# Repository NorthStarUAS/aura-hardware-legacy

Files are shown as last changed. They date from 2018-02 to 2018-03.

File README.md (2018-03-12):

# AuraUAS Autopilot Hardware

This is a repository of hardware designs that have evolved out of the
AuraUAS project.  These designs serve the AuraUAS ecosystem.

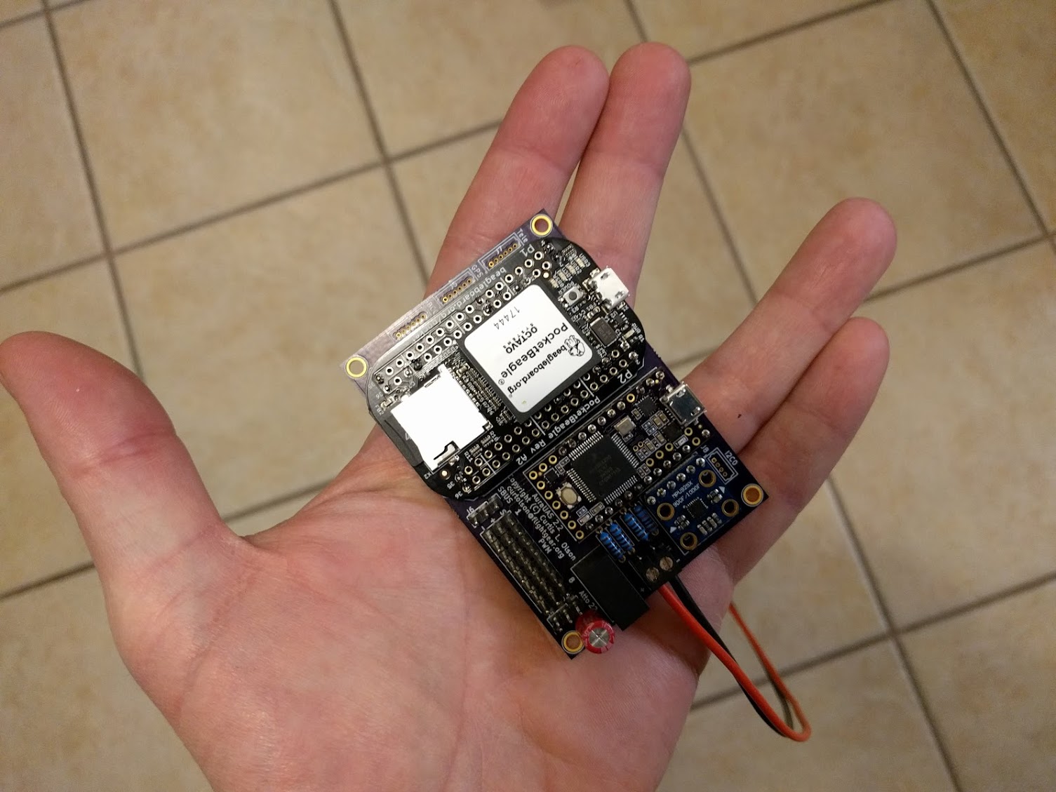
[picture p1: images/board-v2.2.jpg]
map Version 2.2 Build


## Version 1.0 - 1.4 (May 2015 - August 2016)

Beaglebone Black + Custom Cape + APM2

This is the first functional autopilot board design I created myself.
I have built up at least 4 flying autopilots from this design.
However, it leverages the old APM2 (atmega2560-based) board as the
sensor head.  This results actually are quite good, but it leads to a
stack of 3 boards and a fairly inefficient layout.  Also the APM2 is a
very old design now, has some limitations, and is only available through
clone outlets.

## Version 1.5 (January 2017)

Beaglebone Black + Custom Cape + Teensy-3.2

Although not listed as v1.5 in the file names, this is the logical
successor to the APM2-based board.  The APM2 is dropped and replaced
by a more modern teensy-3.2 paired with an IMU/Pressure breakout
board.  The teensy offers much more CPU power, more memory, better
ADC's, and native 3.3v ttl logic levels.

The system was breadboarded and the overall concept proved out.
However, before this design was finished or built, the pocketbeagle
became available.  This has prompted me to move to the next iteration.

## Version 2.0 - 2.1 (January 2018)

Pocketbeagle + Teensy-3.2 + Custom Board (designed with Express PCB)

This is a single board that combines a pocketbeagle + teensy + imu
breakout + voltage regulator + connectors in a single board package
that has only slightly larger footprint compared to the original
beaglebone.

I ordered a test run of the v2.0 board and built up one to full flight
status.

This board was designed with the Express PCB software which also
requires ordering your boards from Express PCB.  The trade off is ease
of design versus flexibility and cost.

## Version 2.2 (February 2018)

Pocketbeagle + Teensy-3.2 + Custom Board (KiCad + Oshpark)

The next evolution of the board is a redesign in KiCad.  The main
benefit is the ability to order the design from a multitude of board
houses, and possibly even do a pick and place shop at some point in
the future.  This gives the most flexibility and less expensive board
runs.

Oshpark is a great inexpensive option.  They can suck in my KiCad pcb
file directly, and they are open-source and community-sharing
friendly.

Major updates:
- Switch to the awesome KiCad PCB design tool.
- Rearrange and move some parts to shrink the board footprint and
  simplify trace routing.
- Cleans up a few small goof ups in the v2.0 design.
- Switch to the TSR2-2450 power supply (functionally similar but
  slimmer and cleaner looking.)
- Add a voltage divider/sensor circuit for main input battery voltage
  (to complement the regulated voltage sensor.)
- Switch to a robust screw terminal connector for main power.

## Version 2.3 (March 2018)

Pocketbeagle + Teensy-3.2 + 2 Layer Custom Board (KiCad + Oshpark)

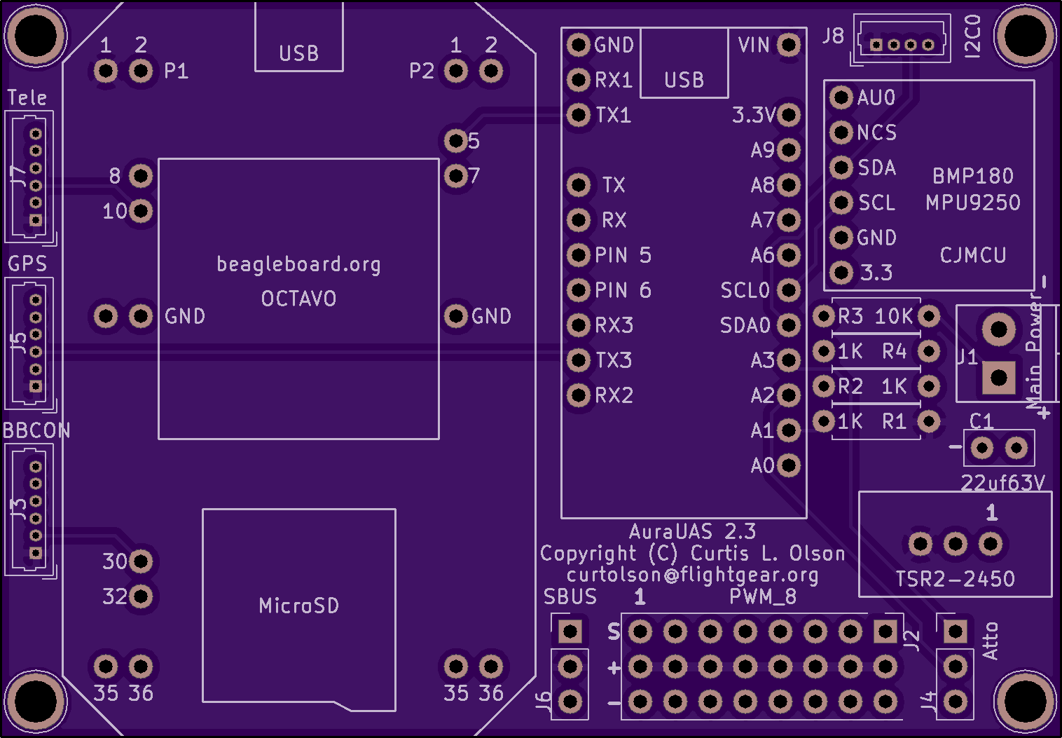
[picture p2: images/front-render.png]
map Front of board


Major updates:
- Reverse TX/RX on GPS and Telemetry ports to match drone code
  standard (big dohhh!!! while assembling the first v2.2 board)
- Slide screw terminal slightly towards board edge to give more space
  to the resistors.
- Clearly mark pin 1 on TSR2-2450 connector to help avoid assembly
  mistakes.
- Relocate capacitor away from corner mounting hole.
- Draw bigger usb port outlines on teensy/pocketbeagle to match reality.
- Space sbus and atto connectors exactly 0.2" from ends of PWM block.-
  Experiment with KiCad's autorouting feature.
- Many small component placement and trace routing adjustments for better
  fit and aethsetics.

## Overview

These board designs support the AuraUAS autopilot flight code and
firmware.  The goal is to offer a relatively simple DIY "kit build"
solution for fixed wing UAV autopilots.  Attention is put towards
using inexpensive, but powerful off the shelf components.  Assembly is
relatively simple (mostly 0.1" header soldering.)  Overall cost is
comparable to other small UAV autopilot systems.

The basic architecture of the system employs a 'little' processor and
a 'big' processor working together as a distributed system.  The
little processor handles all the hard real time sensor I/O tasks.  The
big processor does all the heavy lifting, ekf, control, navigation,
logging, communication, and higher level logic and functions.

This system has been developed based on experience with UAS flight
control hardware, software, and flight test experience starting around
2005.  There is a fair bit of thought, experience, different ideas
tried, and lessons learned the hard way that have gone into the design
choices, development, and tuning of this system.

The following information needs to be reviewed and updated, but is
still mostly reliable.

## Primary design goals

- Maximize use of existing mature, inexpensive, and widely available
  sub-components.
- Minimize amount of custom electronic circuits, soldering, and cabling.
- Easy assembly/fabrication from kit (mostly 0.1" header soldering.)
- Minimize external wiring rats nest by pushing as many connections as
  possible onto the cape.
- High performance, high reliability, production quality flight
  results.

## Features

- Beaglebone/Linux based flight control system (big processor).
- Teensy/arduino based sensor interface (little processor.)
- SBUS RC Inputs (SBUS receiver required)
- 8 PWM Outputs (PWM servos required)
- MPU-9250 IMU, BMP[12]80 pressure sensor.
- 5v 2A power regulator on board.
- Attopilot (volt/amp) sensor interface for main battery.
- Avionics/main voltage sensing on board.
- Pocketbeagle console UART exposed.
- Supports industry standard (mRo) external devices: ublox 8 gps,
  900mhz radio modem, i2c based airspeed sensor.
- Mature firmware, autopilot flight code, and ground station interface.

## Power

- Input power can be anything that ranges from 6.5-36 volts.
- The board includes a 5V 2A regulator to provide clean stable power
  for all the avionics (pocketbeagle, teensy, gps, telemetry, RC
  receiver, etc.)
- Servos are powered from some external source arranged by the
  integrator (for example from the ESC via the throttle channel.)

## Communication

- Supports a variety of 5v (3.3v TTL) radio modems such as Freescale,
  mRo, and Digi Xtend.
- Exposes the mini-usb port on both the Teensy and the Pocketbeagle
  for updating firmware or debugging.
- Exposes the beaglebone UART0 (console) for additional communication
  and/or debugging the beaglebone.

## Cost

This board is not available for sale as an assembled unit.  However,
you are welcome to download the design and order it through Oshpark
(or any other board service.)  You can purchase all the components and
populate the board yourself with only minimal soldering skills.  I
estimate it will cost about $100/ea to assemble a full board.  Most
items can be purchased with free shipping.

The external components such as gps, radio modem, receiver, attopilot
volt/current sensor, etc. need to be purchased separately.  These are
things that are required for any autopilot system.

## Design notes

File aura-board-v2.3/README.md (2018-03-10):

# AuraUAS Autopilot Board

## Assembly Instructions and Check List

I recommend you print out these instructions on paper and actually
check off each step as it is completed.  Some steps cannot be
completed out of order!  If you work carefully and don't need to
resolve any major goof ups, I think most people can do this assembly in
2-3 evenings.

### Tools required

- [ ] A nice solder station such as a Weller WES51.  Right now I like
  600-650F for soldering 0.1" header pins.
- [ ] A volt meter and continuity checker.
- [ ] A small clipping pliers / wire cutter.
- [ ] Needle nose pliers.
- [ ] Lighted magnifying lens (if over 40.)
- [ ] 6.5 - 36V power supply.  I have a bench power supply from Extech
  that allows me to vary the voltage and shows me the current draw,
  but a battery or simple wall wart could work fine too.

### Install Power Subsystem

- [ ] Install 3.5mm screw terminal block.
- [ ] Install TSR2-2450 voltage regulator.  Note: pin 1 on the
  TSR2-2450 has a white dot next to it.  This corresponds with the
  hole nearest the edge of the board.
- [ ] You can go ahead and power up the board at this point (I
  recommend using < 20 volt supply until the capacitor is installed.)
  Using the schematic and board layout, test all the 5v points to make
  sure power is getting to the correct locations.
- [ ] Install the 22uf63v capacitor being careful to note polarity.
- [ ] Install the 3 x 1k ohm resistors. You might find a needle nose
  pliers helpful to gently pull on the wires from the back side and
  help the resister fully seat in place.
- [ ] Install the 10k ohm resistor.  Polarity does not matter with
  resistors.  Clip off the excess wire from the back of the board.
- [ ] Go ahead and power up the board again.  Test that pin-hole A0 on
  the teensy footprint reads about 1/11 of your input voltage.  Test
  that pin-hole A1 reads about 2.5 volts.

### Install the Teensy-3.2

- [ ] Carefully scratch between the two pads on the reverse side of
  the board to disable USB power to the teensy.  This is important
  because the teensy-3.2 is not tolerant of being powered by both usb
  and onboard power simultaneously.
  - If you forget this step before installing the teensy, there is no
    way to fix it!  But there is a work around ...
  - The recommendation is to rig up a standard USB cable with
    the red power line snipped and still safely upload firmware to your
    teensy while it is powered by the board regulator.
  - It is just annoying because you have to remember to use the
    correct usb cable or you may significantly shorten the life of your
    teensy.
  - I recommend you clearly mark the usb port on the teensy to remind
    yourself to always use your special non-power usb cable.
- [ ] Clip rows of 0.1" header pins to fill the available holes
  between the teensy and the AuraUAS board.
- [ ] Test fit the teensy, making sure you are not shifted up or down
  by one pin.  The teensy should be centered on the footprint outline
  drawn on the board.  The teensy usb port should be at the top edge
  of the board as shown in the footprint outline.
- [ ] Carefully solder all the pins from the top side.
- [ ] Last chance!  Make sure you scratched apart the two pads on the
  bottom of the teensy.
- [ ] Flip the board over and carefully solder all the pins from the
  bottom side.
- [ ] Use your wire cutter to carefully clip all the excess length of
  the back side pins off the board.
- [ ] Power up the board.  A stock teensy should blink it's LED light
  about once per second if it is getting power properly.
- [ ] Test that you are reading 3.3 volts at the MPU-9250 breakout
  board 3.3 pin hole.
- [ ] You can install the teensy-3.2 firmware (aura-sensors) now if
  you wish or wait until later.

### Install the CJMCU MPU-9250 breakout board

- [ ] Follow the same basic technique used for the teensy.
- [ ] Clip a continuous row of 5 x 0.1" header pins (The breakout
  board may come with pins.)
- [ ] Carefully position the board (supporting the side opposite of
  the pins with a spare header pin on it's side) and solder the pins
  from the top of the board. Note that it may be a tight fit depending
  on which board you get.
- [ ] Flip the board over and solder the back side pins.  *Important:*
  be careful to ensure the breakout board is as flush as possible and
  square with the AuraUAS board. Your IMU is on this board so it the
  more accurately you place this board, the better life will be when
  it comes time to fly.
- [ ] Don't forget to clip off the excess pin material on the back
  side of the board.
- [ ] Now you can power up the board and test the firmware is able to
  read the IMU!

### Install the Pocketbeagle

- [ ] Follow the same basic procedure as the teensy and the IMU
  breakout boards.
- [ ] Clip individual and pair-wise 0.1" pins to fill in the pin-holes
  that are used by the teensy.  8 x 2-pin pairs + 1 individual pin is needed.
- [ ] Carefully position the pocketbeagle on the board.  Before
  soldering, make sure the pocketbeagle is lined up with the footprint
  lines, the usb port is facing the top side of the board, and that
  there are no missing pins.  Now go ahead and solder the pins from
  the top side.
- [ ] Flip the board over and solder the pins from the backside.  Then
  clip off the excess pin length.
- [ ] Go ahead and power the board up again.  The pocketbeagle has a
  blue led that should light up.
- [ ] If you have an SD card prepared, you can insert it and fully
  boot up the pocketbeagle, connect to a laptop via the usb port, log
  in like it's any other beaglebone in the world, and you should be do
  all sorts of linux stuff.

### Install the RC Connectors

- [ ] Clip off 3 strings of 8 x 0.1" headers to complete the PWM
  output block.  Solder these on from the back.  A servo connector
  plugged into one or both ends can really help keep their alignment
  right on while you solder them in.
- [ ] Clip off 2 strings of 3 x 0.1" headers for the SBUS input
  connector and the Attopilot connector.  Solder these in.  I often try
  to block up the connector is it is positioned correctly.  Then I
  solder one pin and check for position and alignment.  If anything is
  off I can reheat that one pin and fix it.  Then once everything is
  double checked good and lined up and in the right place, I finish
  soldering the remainder of the pins.

### Install the Picoblade (or DF-13) connectors.

Integrator's choice of connectors here.  Sorry that JST-GH doesn't
have a through-hole variant so we are stuck with one of these other
connectors.  mRobotics should have JST-GH -> Picoblade and JSG-GH ->
DF-13 cables available, so pick your favorite and go with it.

These connectors have 1.25mm spacing so they are a bit trickier than
the 0.1" inch connectors.  Just be super careful, use a small bit of
solder, and remember heat and surface tension should make the solder
go where it needs to go and no further.  Be careful not to slather in
too much solder and bridge two adjacent pins!

Again, I recommend doing your best to block up and align the
connector, then solder just one pin.  Carefully check position and
alignment.  It's easy to reheat that one pin and make adjustments.
When you are happy, solder the remaining pins.

- [ ] Install the 6-position telemetry and gps connectors.  (Note the
  board can support soldering a 5-position connector.  You can review
  the schematic and board layout to figure out the proper position.)
- [ ] Install the 4-position i2c connector.  Again, mRobotics is your
  cable adapter friend.
- [ ] Optionally install the 6-position BBCON connector.  This gives
  you access to the Pocketbeagle console for debugging or possibly
  another uart for some future use.

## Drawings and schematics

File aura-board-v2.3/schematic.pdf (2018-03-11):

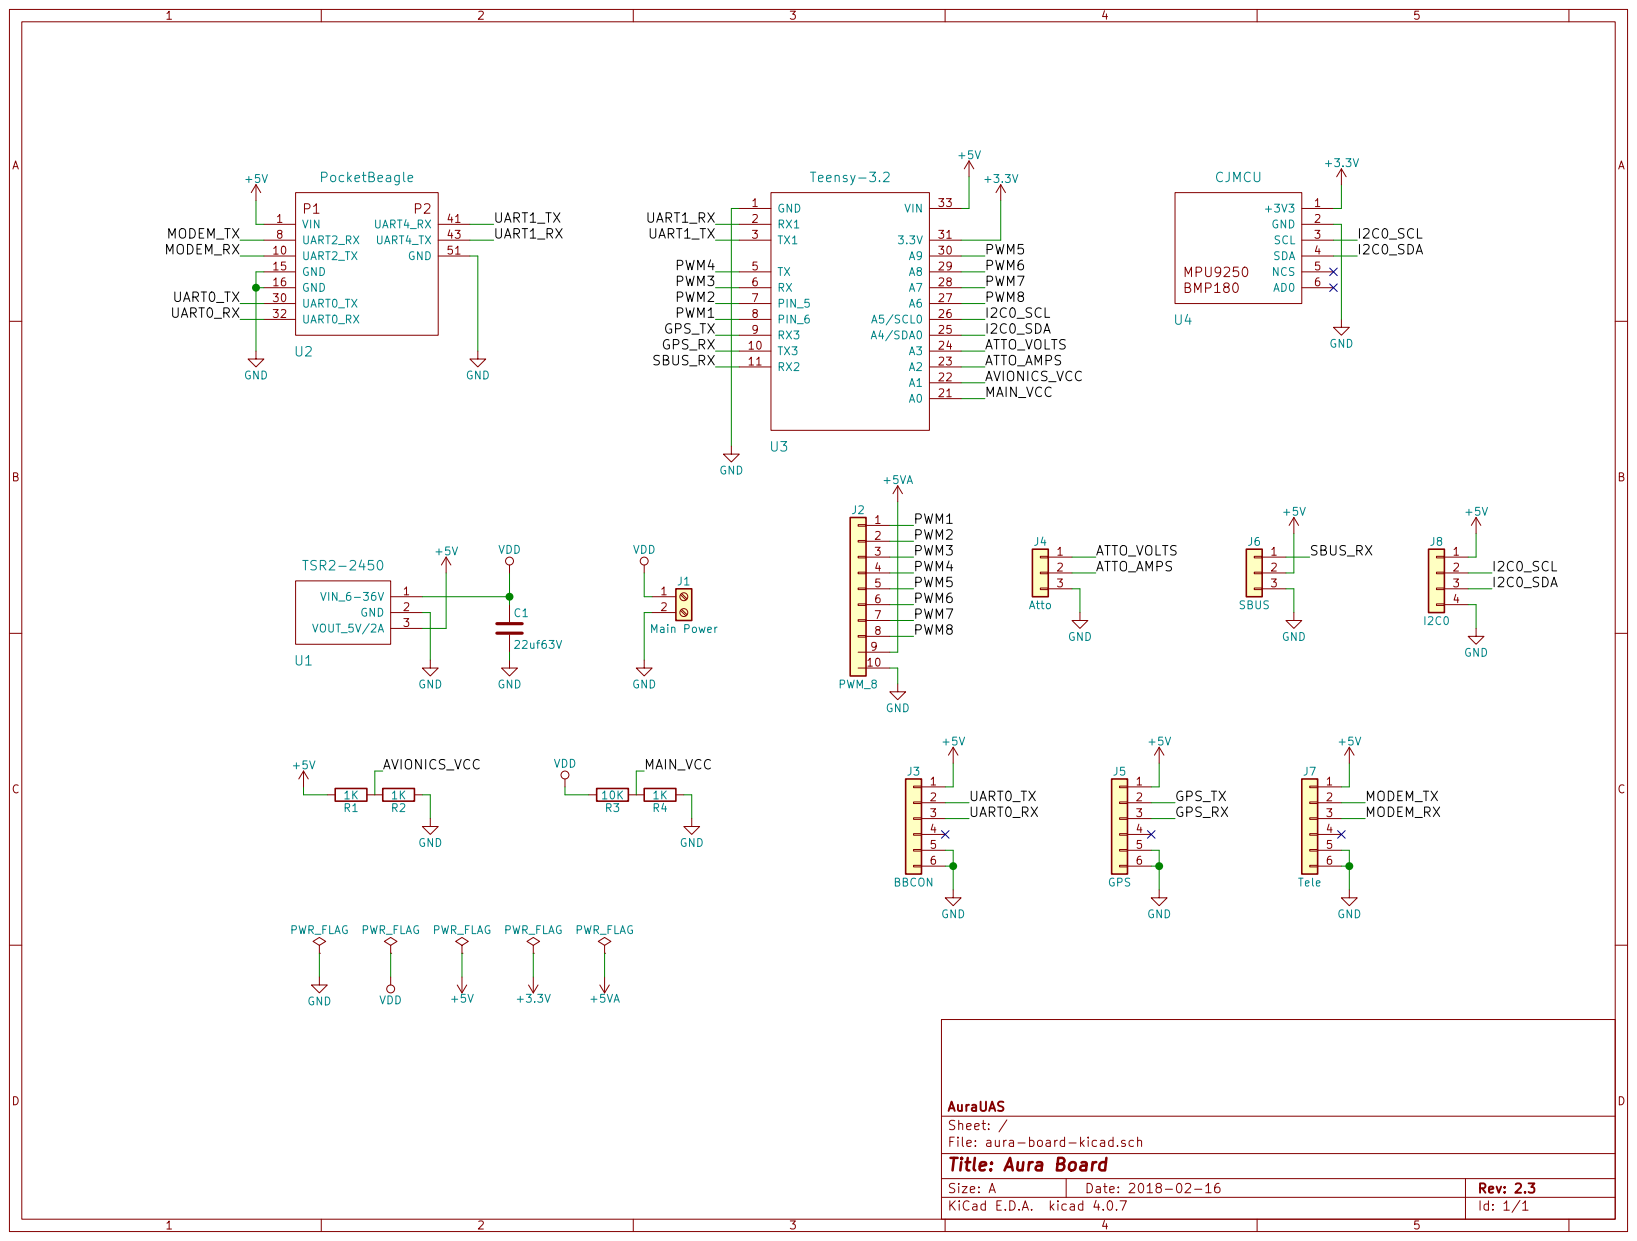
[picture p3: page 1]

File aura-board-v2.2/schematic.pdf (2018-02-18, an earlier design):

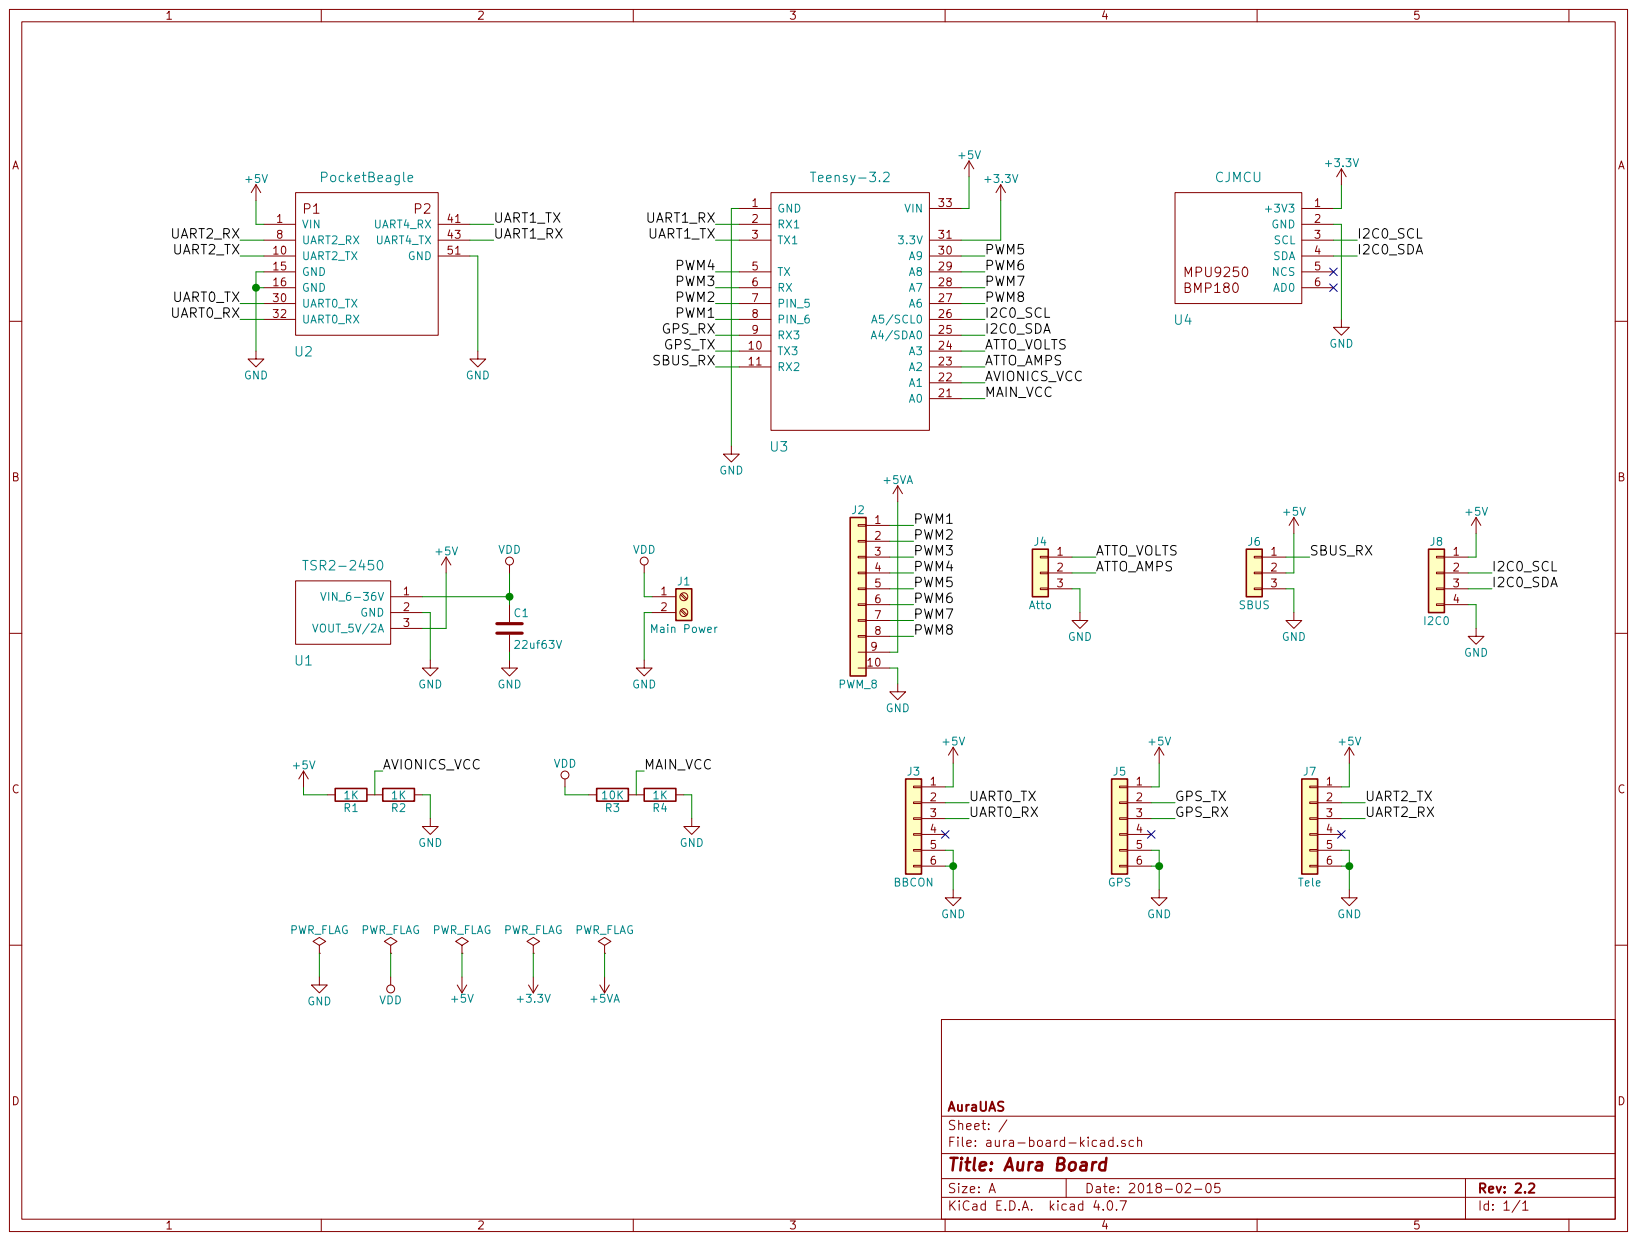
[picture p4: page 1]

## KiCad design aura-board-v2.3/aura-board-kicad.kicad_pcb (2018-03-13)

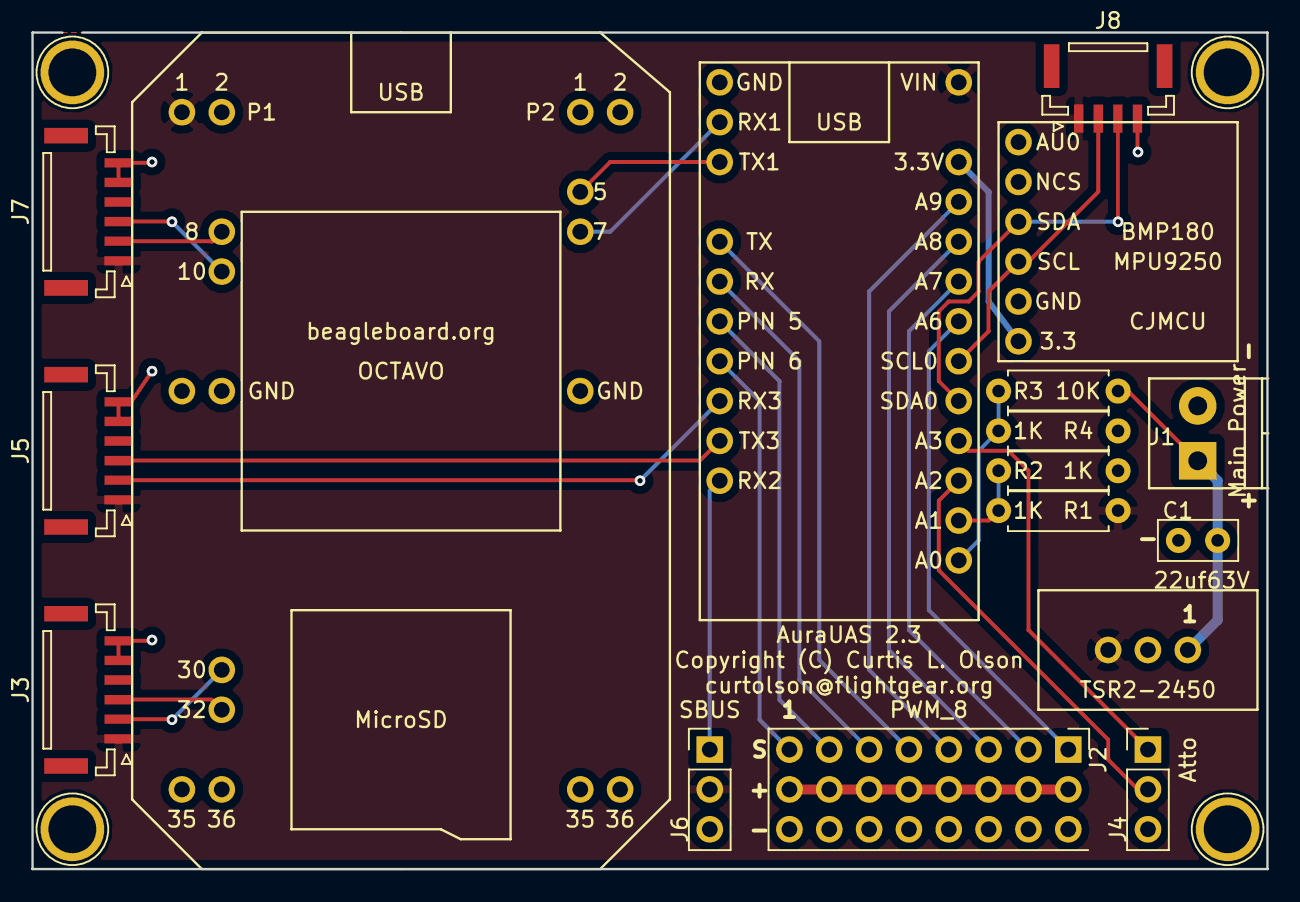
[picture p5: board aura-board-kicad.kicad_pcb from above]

Board: 2 copper layers, 78.7 x 53.3 mm, 21 parts (0 on the bottom side), 27 nets.

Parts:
C1: 22uf63V; C_Disc_D5.0mm_W2.5mm_P2.50mm
J1: Main Power; TerminalBlock_Pheonix_PT-3.5mm_2pol
J2: PWM_8; PWM_3x08
J3: BBCON; JST_GH_BM06B-GHS-TBT_06x1.25mm_Straight
J4: Atto; Pin_Header_Straight_1x03_Pitch2.54mm
J5: GPS; JST_GH_BM06B-GHS-TBT_06x1.25mm_Straight
J6: SBUS; Pin_Header_Straight_1x03_Pitch2.54mm
J7: Tele; JST_GH_BM06B-GHS-TBT_06x1.25mm_Straight
J8: I2C0; JST_GH_BM04B-GHS-TBT_04x1.25mm_Straight
MH1, MH2, MH3, MH4: 1pin
R1, R2, R4: 1K; R_Axial_DIN0207_L6.3mm_D2.5mm_P7.62mm_Horizontal
R3: 10K; R_Axial_DIN0207_L6.3mm_D2.5mm_P7.62mm_Horizontal
U1: TSR2-2450
U2: PocketBeagle
U3: Teensy-3.2
U4: CJMCU

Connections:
+3V3: U3.31, U4.1
+5V: J3.1, J5.1, J6.2, J7.1, J8.1, R1.2, U1.3, U2.1, U3.33
/ATTO_AMPS: J4.2, U3.23
/ATTO_VOLTS: J4.1, U3.24
/AVIONICS_VCC: R1.1, R2.2, U3.22
/GPS_RX: J5.3, U3.10
/GPS_TX: J5.2, U3.9
/I2C0_SCL: J8.2, U3.26, U4.3
/I2C0_SDA: J8.3, U3.25, U4.4
/MAIN_VCC: R3.1, R4.2, U3.21
/MODEM_RX: J7.3, U2.10
/MODEM_TX: J7.2, U2.8
/PWM1: J2.1, U3.8
/PWM2: J2.2, U3.7
/PWM3: J2.3, U3.6
/PWM4: J2.4, U3.5
/PWM5: J2.5, U3.30
/PWM6: J2.6, U3.29
/PWM7: J2.7, U3.28
/PWM8: J2.8, U3.27
/SBUS_RX: J6.1, U3.11
/UART0_RX: J3.3, U2.32
/UART0_TX: J3.2, U2.30
/UART1_RX: U2.43, U3.2
/UART1_TX: U2.41, U3.3
GND: C1.2, J1.2, J2.10, J3.5, J3.6, J4.3, J5.5, J5.6, J6.3, J7.5, J7.6, J8.4, R2.1, R4.1, U1.2, U2.15, U2.16, U2.51, U3.1, U4.2
VDD: C1.1, J1.1, R3.2, U1.1

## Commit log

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2015-06-04 After checking out DF13 connections now that cables arrived, I discovered that TX/RX were reversed on the APM2 connection. This is fixed in both the 1.0 and the 1.1 versions of the board.
    On the radio modem connector I had grounded both pins 5 and 6 to accept
    either a 5 or 6 position connector, but upon testing, if this is grounded
    on a 6 position cable, it puts the radio modem into bootloader mode, so
    I have removed the grounding connection on pin 5. A 5 position connector
    could still be used with a bit of extra work on the backside to ground pin 5.
2015-06-05 Shift apm mounting holes slightly aft to give a bit more clearance from the bb power barrel connector up front.
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2015-06-08 Final changes before ordering 3 miniboards. (Including a JST-PH-2 power connector if I didn't mention that earlier.)
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2015-12-09 Shrink ground plane so it doesn't extend to edge of board. Integrate Pololu D24V22F5 (5.0v 2.0 amp voltage regulator) Remove APM2-mini support (didn't like the hydra of cheap wires it included.)
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2017-08-03 Roughing in a schematic for a new cape. This one would drop the legacy APM2 board and replace it with a Teensy-3.2 and MPU-9250 breakout board. The net result should be cleaner with far better perfor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
    [newcape-3.2.sch]
2017-08-03 Clean up a few connection routes.
    [newcape-3.2.sch]
2017-08-03 Added an 'abbreviated' beaglebone P9 header to schematic.
    [newcape-3.2.sch]
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2017-08-04 Added voltage divider resistors for measuring avionics and main voltages.
    [newcape-3.2.sch]
2017-08-06 Add external I2C connector and GPS-UART connector.
    [newcape-3.2.sch]
2017-08-06 Various cleanups and tweaks and rearrangements.
    [newcape-3.2.sch]
2017-08-07 A few more tweaks in the process of forever tweaking.
    [newcape-3.2.sch]
2017-08-07 Add attopilot connector (to two analog inputs.)
    [newcape-3.2.sch]
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2018-01-11 Initial revision of a pocketbeagle/teensy single board AP.
    [aura-board-2.0.sch]
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2018-01-11 Fix the pololu regulator component Add stripped down versions of teensy and pocketbeagle components.
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2018-01-13 Added external i2c connector (4x1 0.1" header). Currently not powered because I don't know if it should be 5v or 3.3v power to an external device?
    Flipped the SBUS and ATTO external connectors to align ground/signal with
    other connectors.
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2018-01-20 Switch to I2C pressure sensor and drop the idea of using the old 5v analog MPXV7002DP differential pressure sensors. The teensy doesn't support 5v analog range, only 3.3v. Mrobotics and BFS both make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
2018-02-01 Starting v2.1: - Somehow after moving the teensy, I never got the ground pin connected to the back plane, now fixed. - Picked too small holes for the MPU-9250 breakout, now fixed. - More updates to c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
2018-02-02 Begin some mods based on experience with first board run.
    - Shift everthing up to the "top" edge of the board for less wasted space.
    We are going to try to shrink the layout in both dimensions.
    - Other planned changes:
    o Switch to a screw terminal block for main power in.
    o Drop the pololu voltage regulator and Switch to a TSR 2-2450 voltage
    regulator (with 22uf 63v capactor.) This should yield a smaller foot
    print and cleaner looking design.
    o Possibly rotate the alignment of the IMU
    o Rework external 1.25mm connector and pins to reduce future cable surgery
    needs.
    o Move the voltage regulator below the teensy and the 3xN servo pin blocks
    to the right end of the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
2018-02-05 Begin dabbling with a kicad schematic for the next auraboard version.
    [aura-board-kicad.sch]
2018-02-05 Add attopilot connector.
    [aura-board-kicad.sch]
2018-02-06 Add screw terminal for external power hookup.
    [aura-board-kicad.sch]
2018-02-06 Added voltage divider circuits for sensing avionics and main voltages.
    [aura-board-kicad.sch]
2018-02-06 Add capacitor to input power circuit.
    [aura-board-kicad.sch]
2018-02-06 Add one missing (VIN) connection.
    [aura-board-kicad.sch]
2018-02-06 Aligning and spacing on the schematic.
    [aura-board-kicad.sch]
2018-02-06 Attempt to draw power busses correctly in schematic.
    [aura-board-kicad.sch]
2018-02-06 Annotate schematic.
    [aura-board-kicad.sch]
2018-02-06 Nudge white space on the schematic, generate a pdf version.
    [aura-board-kicad.sch]
2018-02-06 Working my way through the process of drawing custom footprints for the layout.
    [aura-board-kicad.kicad_pcb, aura-board-kicad.sch]
2018-02-06 Begin pcb layout arrangment of components.
    [aura-board-kicad.kicad_pcb, aura-board-kicad.sch]
2018-02-06 Fix a wrong units issue.
    [aura-board-kicad.kicad_pcb]
2018-02-07 Start adding a few easy traces.
    [aura-board-kicad.kicad_pcb]
2018-02-07 Shuffle PWM assignment on teensy (schematic) to make tracerouting more convenient. Work on trace routing. (Still need to set up a ground plane and create the power bus.)
    [aura-board-kicad.kicad_pcb, aura-board-kicad.sch]
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2018-02-07 Add a ground plane.
    [aura-board-kicad.kicad_pcb]
2018-02-07 More trace routing and tweaking.
    [aura-board-kicad.kicad_pcb]
2018-02-07 More trace routing. Position resistors for voltage divider/sending circuits. Add mounting holes (3mm).
    [aura-board-kicad.kicad_pcb]
2018-02-07 Add a +5V power bus plane on the top layer.
    [aura-board-kicad.kicad_pcb]
2018-02-07 Add pin headers to complete pwm header block.
    [aura-board-kicad.kicad_pcb]
2018-02-07 Add a proper 3x08 PWM block with ground pins and the power bus tied together but not connected to board power.
    [aura-board-kicad.kicad_pcb, aura-board-kicad.sch]
2018-02-07 Swich to picoblade 1.25mm external connectors. DF-13 will also fit here. Pins 5 and 6 both tie to ground. This means the assembler can pick 5 or 6 pos headers depending on their needs. This offers so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
    [aura-board-kicad.kicad_pcb, aura-board-kicad.sch]
2018-02-07 Increase pad diameter (inner and outer) on all my project footprints to match standard 0.1" pin dimensions.
    [aura-board-kicad.kicad_pcb, aura-board-kicad.sch]
2018-02-08 Clean up a small mess after trying to change pad size on all my custom footprints.
    [aura-board-kicad.kicad_pcb]
2018-02-08 Move some of the F.Fab labels to F.SilkS so they show up on the final board.
    [aura-board-kicad.kicad_pcb]
2018-02-08 Make picoblade 6-pos aux-ground pin trace connection slightly thicker.
    [aura-board-kicad.kicad_pcb]
2018-02-08 Add my name and board version to the silkscreen.
    [aura-board-kicad.kicad_pcb]
2018-02-08 Slightly painful, but I moved the teensy 0.05" away from the pocketbeagle to make sure they aren't so close together there is a chance they would conflict. This led to quite a bit of cascading work w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
    [aura-board-kicad.kicad_pcb]
2018-02-08 labelling tweaks.
    [aura-board-kicad.kicad_pcb]
2018-02-08 Label adjustments.
    [aura-board-kicad.kicad_pcb]
2018-02-08 Switch to a larger (3.5mm) screw terminal block for main power.
    [aura-board-kicad.kicad_pcb, aura-board-kicad.sch]
2018-02-08 Project file / directory structure renaming for better clarity.
    [aura-board-2.0.sch, aura-board-kicad.kicad_pcb, aura-board-kicad.sch]
2018-02-08 More renaming of directory layout.
    [aura-board-2.0.sch, aura-board-kicad.kicad_pcb, aura-board-kicad.sch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]
2018-02-08 Small labelling tweak.
    [aura-board-kicad.kicad_pcb]
2018-02-08 A few small tweaks with labeling. Nudge one connector and a couple traces.
    [aura-board-kicad.kicad_pcb]
2018-02-09 Endless tiny tweaks and adjustments continue ...
    [aura-board-kicad.kicad_pcb]
2018-02-10 Follow the standard drone-code pin order for external connectors. Fiddle with a couple traces to hopefully shorten and simplify.
    [aura-board-kicad.kicad_pcb, aura-board-kicad.sch]
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2018-03-02 Starting point for v2.3 improvements.
    [aura-board-kicad.kicad_pcb, aura-board-kicad.sch]
2018-03-10 Initial v2.3 design fixes and tweaks: - reverse tx/rx on gps and telemetry (big dohhh!) - slide screw terminal slightly towards board edge - mark pin #1 on TSR2-2450 connector clearly - relocate capa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
    [aura-board-kicad.kicad_pcb, aura-board-kicad.sch]
2018-03-10 Bump up the version number in the board label Fiddle with traces a bit more.
    [aura-board-kicad.kicad_pcb]
2018-03-10 Various small positional adjustments to give better clearance for the upper right mounting hole. Various trace route tweaks for aesthetics.
    [aura-board-kicad.kicad_pcb]
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2018-03-13 Switch to JST-GH surface mount connectors.
    [aura-board-kicad.kicad_pcb, aura-board-kicad.sch]

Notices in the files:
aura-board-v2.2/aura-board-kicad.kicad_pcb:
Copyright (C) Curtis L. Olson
